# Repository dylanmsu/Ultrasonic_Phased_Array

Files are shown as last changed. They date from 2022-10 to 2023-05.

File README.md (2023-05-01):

# Ultrasonic_Phased_Array
This repository is under construction and will contain all the sources for a working ultrasonic phased array.
The vitis project in this repository is to be used in a accoustic levitation example.

## Working principle
Lets consider an example where we want to send a single pulse of airpressure to a certain point in space. We have an array of transducers we can work with. Since the waves travel in a sphere around the transducers, we can time the pulses at each transducer in such a way that all the wavefronts arrive at the same time in a single focal point. This is illustrated in the animation below.

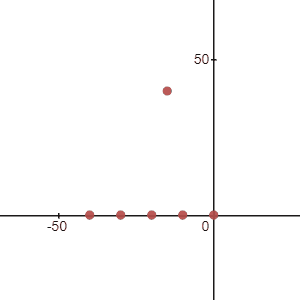
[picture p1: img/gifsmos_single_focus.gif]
[]()

If we were to send a sinewave with the same delay through the transducers instead of a single pulse, all the peaks and troughs of those waves would ideally only add up in the focal point. The amplitude would then be the greatest at that point and ideally cancel out everywhere else. This is actually not always the case because a side effect of using a periodic signal is that we create te posibility of sidelobes. Sidelobes are areas where some of the sinewaves constructively add up unwantedly where the phase shift is a multiple of 360 degrees. To prevent the occurance of sidelobes, we need to space the transducers with a distance between 1/2 wavelength, and 1/4 wavelength. 

To calculate the phase offsets per transducer for a single focal point, the following formula is used:
$$\varphi =  -\frac{2\pi\sqrt{(X_t - X_f)^2 + (Y_t - Y_f)^2 + (Z_t - Z_f)^2}}{\lambda}$$
Where: 
- $\varphi$ = the phase offset for a given transducer
- $X_t, Y_t, Z_t$ = the location of the transducer
- $X_f, Y_f, Z_f$ = the location of the focal point
- $\lambda$ = wavelength

The waves exiting the transducers will look something like this.

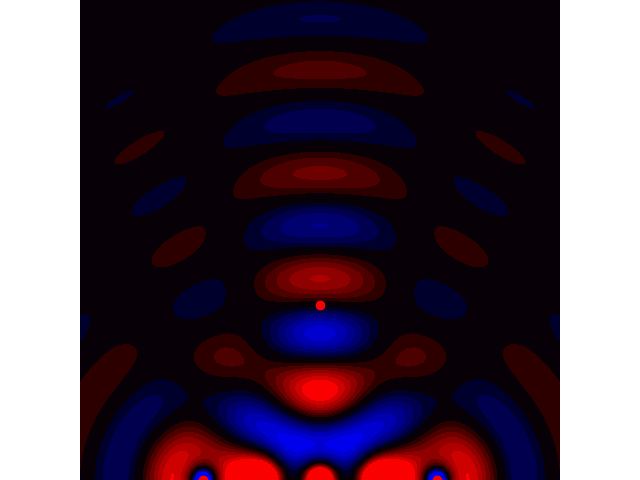
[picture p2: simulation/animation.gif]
[]()

The red dots at the bottom are sources emitting pure sinusodial signals with an adjusted phase delay so all the waves are in phase at the red dot around the middle.

There is an included python script called 'wave_equation.py' that focuses the waves to your mouse location by manipulating the phases of the emitters. It solves the 2d wave equation so it should be more acurate than the above animation.

We can also steer a beam into a specified direction. To do this we have to align the wavefronts into a plane where its normal vector points to the direction of travel. This is illustrated in 2d in the animation below. 

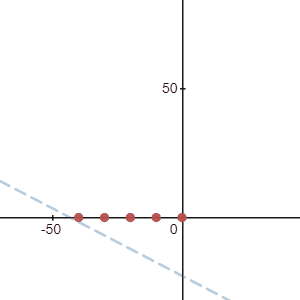
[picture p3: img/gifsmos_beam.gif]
[]()

Here the phase offsets are calculated using the following formula:
$$\varphi = \frac{2\pi(aX_t+bY_t-Z_t)}{\lambda\sqrt{1+a^2+b^2}}$$
Where: 
- $\varphi$ = the phase offset for a given transducer
- $X_t, Y_t, Z_t$ = the location of the transducer
- $a$ = the slope of the tangent plane in the x-axis
- $b$ = the slope of the tangent plane in the y-axis
- $\lambda$ = wavelength

The waves exiting the transducers will look something like this.

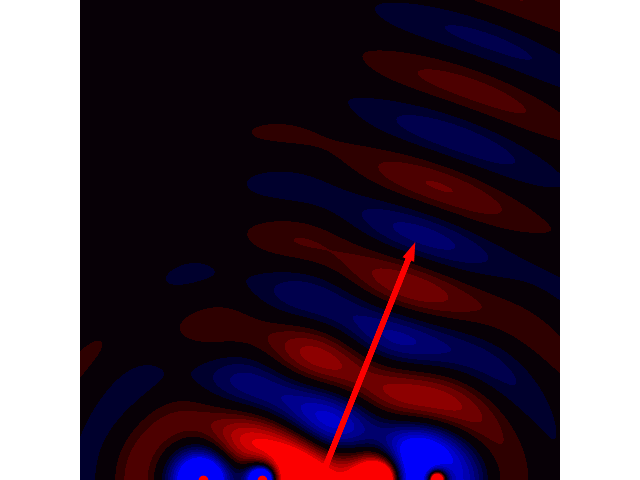
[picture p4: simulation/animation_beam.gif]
[]()

In the case for this project, the spacing between the sources is 10 mm wich is more than double the recommended wavelength so we expect some loss of energy through sidelobes. Even more so diagonally since the sources are placed in a rectangular grid and the diagonal spacing is 14.14 mm. Placing the sources in a hexagonal grid solves big diagonal spacing but this makes the design of the PCB more challanging. For this reason i opted to design a rectangular grid of sources anyway.

## Setup
There are two array's used in the levitation example. One is facing upwards and the other is facing downwards. They are facing eachother with a distance of 70mm. This distance is arbitrarily chosen based on the needed volume for levitation.

## FPGA
The FPGA used in this project is the ZYNQ XC7Z020 on a Zybo Z7 board but any Zynq FPGA should work. The FPGA contains two distinct parts: The processing system (PS) and the programmable logic (PL):

### Programmable Logic
The PL contains an implementation which receives 7 bit values from the PS (Processing System) for every transducer. This value sets the phase of the output signal. This is acheived by making a fifo of length = 2^7 in the case of a phase resolution of 7 bits. The 40KHz signal is fed into the fifo at 40KHz * 2^7 = 5.12MHz. The reason for this is because we want exactly 1 full period of the signal in the fifo. The 7 bit value determines at which address of the fifo the output signal is tapped from. This way wan can adjust the phase of the output signal in 2^7 steps per period.

The block diagram that takes an AXI peripheral bus and outputs a serial data stream to drive the included transducer board is illustrated below. 

[]()

here is an overview of the in- and output signals:
- **signal_in**: this is the signal that will drive the transducers and whos phase will be altered, in our case this signal would have a 50% dutycycle at 40KHz.
- **fifo_clk**: this is the clock that shifts the fifo's used for the delay generation. This should be 2^7 times faster than the 40KHz signal. in this case the fifo length and so the phase resolution is 2^7. This means a frequency of 5.12MHz.
- **ser_clk**: this is the serial clock that drives the serializer and also the shift registers on the transducer board. This clock should be 5x the 'fifo_clock' if each shift register drives 5 transducers. This means a frequency of 25.6MHz.
- **s00_axi_aclk**: this is the AXI peripheral clock comming directly from the Processing system.
- **en**: enable the output signal.
- **resetn**: active low reset signal.
- **S00_AXI**: AXI slave port
- **pmod_out**: this port goes directly to a Pmod port on the FPGA-board and drives the transducer board.

The AXI peripheral IP_block generates the delayed signals and outputs them as a 25 bit vector. This vector is split into 5x 5 bit vectors by the xlslice blocks. The 5 bit vectors enter the seializer. The data is then clocked bit by bit to the output.

### Implementation
[]()

TODO

### Processing System
The Processing system sends data to the FPGA facric which adjusts the phase offsets of the physical transducers.

### Practical limitations
In an ideal world the signal applied to the physical transducer should give the same signal in air pressure. That is however not the case. For every transducer there is a significant random phase shift present. This will completely negate our effort to acheive a phased array. So we have to measure the phase shift of every transducer and incorporate this into the phase calculations.

### Video
Below is a video showing two ultrasonic arrays levitating a piece of styrofoam in an preprogrammed path.
<a href="http://www.youtube.com/watch?feature=player_embedded&v=-Alf5AHHJVo" target="_blank">
 Watch the video
</a>

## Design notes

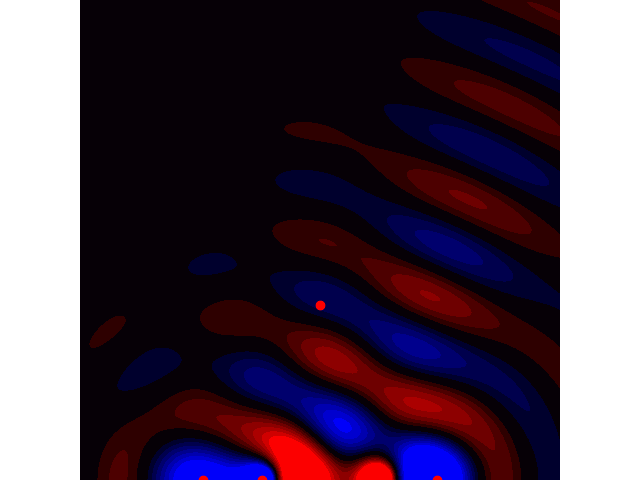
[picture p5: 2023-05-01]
animation_beam.gif

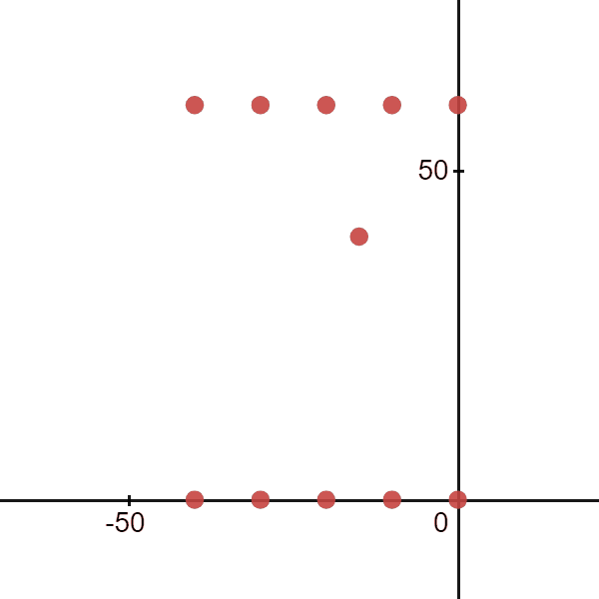
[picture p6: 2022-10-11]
img/gifsmos_double_focus.gif

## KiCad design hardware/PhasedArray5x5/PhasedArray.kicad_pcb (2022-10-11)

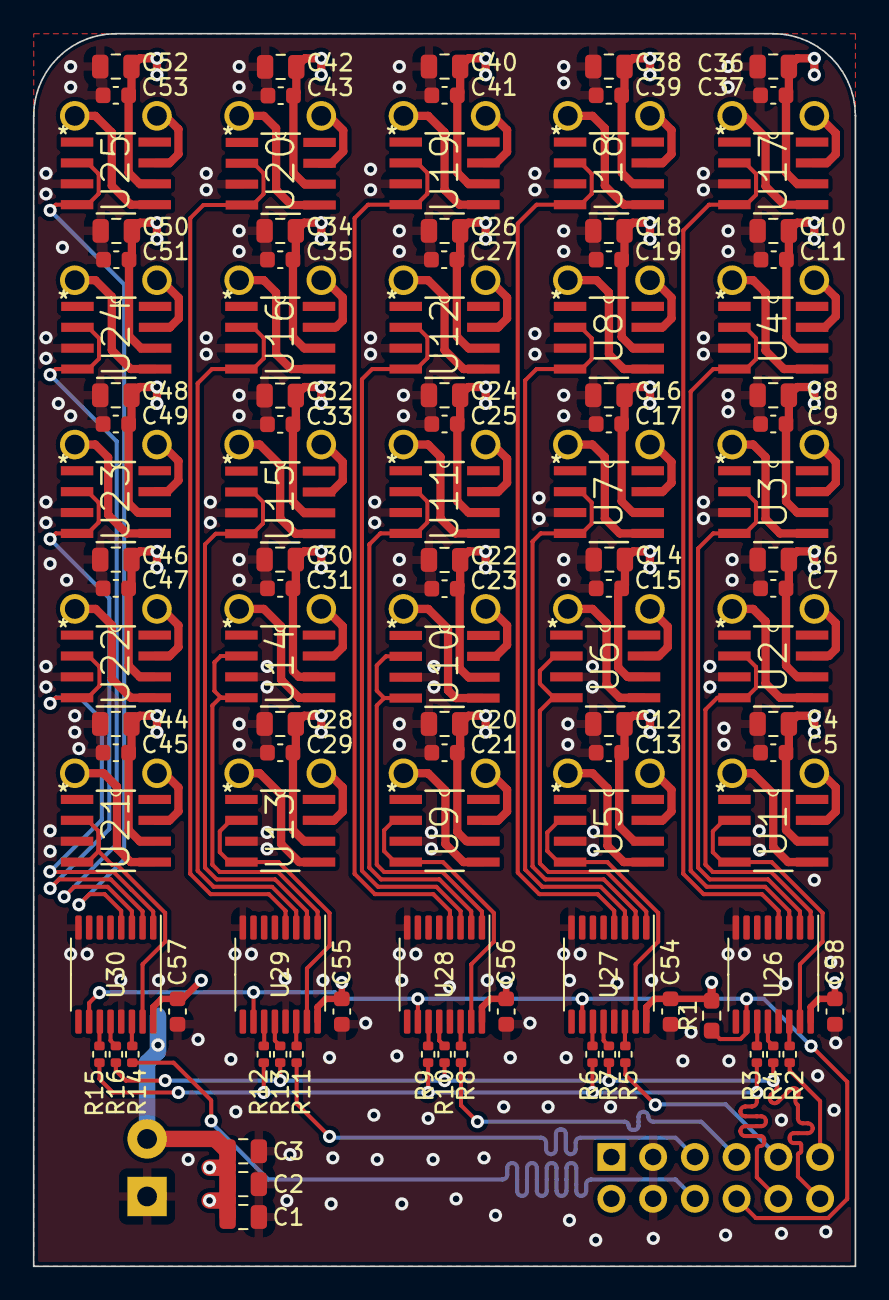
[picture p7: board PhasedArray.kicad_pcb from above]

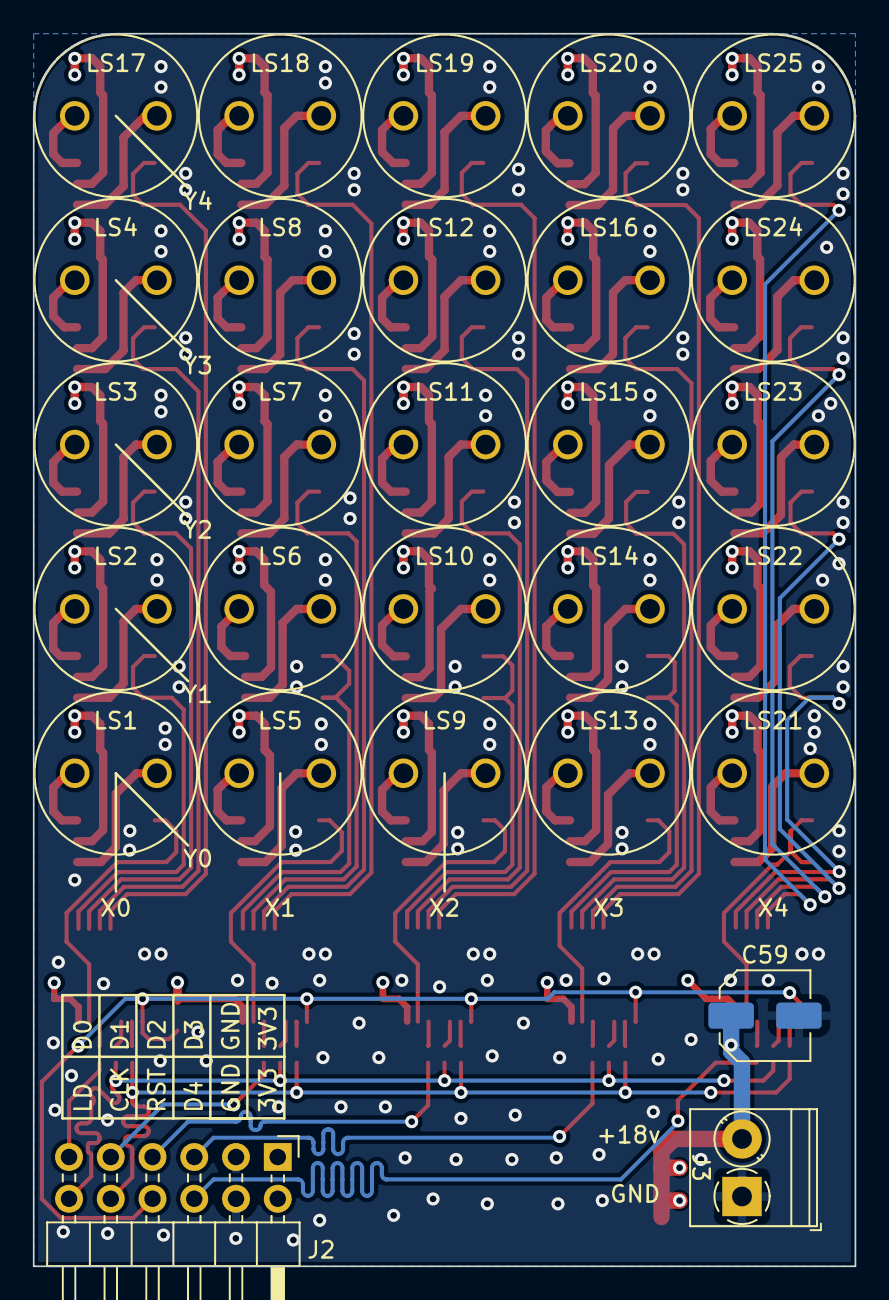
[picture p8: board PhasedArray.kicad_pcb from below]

Board: 4 copper layers, 50.0 x 75.0 mm, 132 parts (28 on the bottom side), 101 nets.

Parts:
C1, C2, C3, C4, C6, C8, C10, C12, C14, C16, C18, C20, C22, C24, C26, C28, C30, C32, C34, C36, C38, C40, C42, C44, C46, C48, C50, C52: 4.7uF; C_0805_2012Metric
C5, C7, C9, C11, C13, C15, C17, C19, C21, C23, C25, C27, C29, C31, C33, C35, C37, C39, C41, C43, C45, C47, C49, C51, C53, C54, C55, C56, C57, C58: 100nF; C_0603_1608Metric
C59: 47uF; C_Elec_5x5.4
J2: Conn_02x06_Odd_Even; PinHeader_2x06_P2.54mm_Horizontal
J3: Screw_Terminal_01x02; TerminalBlock_Phoenix_PT-1,5-2-3.5-H_1x02_P3.50mm_Horizontal
LS1, LS2, LS3, LS4, LS5, LS6, LS7, LS8, LS9, LS10, LS11, LS12, LS13, LS14, LS15, LS16, LS17, LS18, LS19, LS20, LS21, LS22, LS23, LS24, LS25: Speaker_Ultrasound; XDCR_MA40S4R
R1: 0R; R_0603_1608Metric_Pad0.98x0.95mm_HandSolder
R2, R3, R4, R5, R6, R7, R8, R9, R10, R11, R12, R13, R14, R15, R16: 39R; R_0402_1005Metric
U1, U2, U3, U4, U5, U6, U7, U8, U9, U10, U11, U12, U13, U14, U15, U16, U17, U18, U19, U20, U21, U22, U23, U24, U25: TC4428AEOA; SOIC127P600X175-8N
U26, U27, U28, U29, U30: 74AHCT595; TSSOP-16_4.4x5mm_P0.65mm

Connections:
+3V3: C54.1, C55.1, C56.1, C57.1, C58.1, J2.1, J2.2, R1.2, U26.16 (VCC), U27.16 (VCC), U28.16 (VCC), U29.16 (VCC), U30.16 (VCC)
+15V: C1.1, C2.1, C3.1, C4.1, C5.1, C6.1, C7.1, C8.1, C9.1, C10.1, C11.1, C12.1, C13.1, C14.1, C15.1, C16.1, C17.1, C18.1, C19.1, C20.1, C21.1, C22.1, C23.1, C24.1, C25.1, C26.1, C27.1, C28.1, C29.1, C30.1, C31.1, C32.1, C33.1, C34.1, C35.1, C36.1, C37.1, C38.1, C39.1, C40.1, C41.1, C42.1, C43.1, C44.1, C45.1, C46.1, C47.1, C48.1, C49.1, C50.1, C51.1, C52.1, C53.1, C59.1, J3.2, U1.6 (VDD), U2.6 (VDD), U3.6 (VDD), U4.6 (VDD), U5.6 (VDD), U6.6 (VDD), U7.6 (VDD), U8.6 (VDD), U9.6 (VDD), U10.6 (VDD), U11.6 (VDD), U12.6 (VDD), U13.6 (VDD), U14.6 (VDD), U15.6 (VDD), U16.6 (VDD), U17.6 (VDD), U18.6 (VDD), U19.6 (VDD), U20.6 (VDD), U21.6 (VDD), U22.6 (VDD), U23.6 (VDD), U24.6 (VDD), U25.6 (VDD)
CLK: J2.10, R3.1, R6.1, R9.1, R12.1, R15.1
GND: C1.2, C2.2, C3.2, C4.2, C5.2, C6.2, C7.2, C8.2, C9.2, C10.2, C11.2, C12.2, C13.2, C14.2, C15.2, C16.2, C17.2, C18.2, C19.2, C20.2, C21.2, C22.2, C23.2, C24.2, C25.2, C26.2, C27.2, C28.2, C29.2, C30.2, C31.2, C32.2, C33.2, C34.2, C35.2, C36.2, C37.2, C38.2, C39.2, C40.2, C41.2, C42.2, C43.2, C44.2, C45.2, C46.2, C47.2, C48.2, C49.2, C50.2, C51.2, C52.2, C53.2, C54.2, C55.2, C56.2, C57.2, C58.2, C59.2, J2.3, J2.4, J3.1, U1.3 (GND), U2.3 (GND), U3.3 (GND), U4.3 (GND), U5.3 (GND), U6.3 (GND), U7.3 (GND), U8.3 (GND), U9.3 (GND), U10.3 (GND), U11.3 (GND), U12.3 (GND), U13.3 (GND), U14.3 (GND), U15.3 (GND), U16.3 (GND), U17.3 (GND), U18.3 (GND), U19.3 (GND), U20.3 (GND), U21.3 (GND), U22.3 (GND), U23.3 (GND), U24.3 (GND), U25.3 (GND), U26.8 (GND), U26.13 (~OE), U27.8 (GND), U27.13 (~OE), U28.8 (GND), U28.13 (~OE), U29.8 (GND), U29.13 (~OE), U30.8 (GND), U30.13 (~OE)
LOAD: J2.12, R4.1, R7.1, R10.1, R13.1, R16.1
unnamed: LS1.1, U1.7 (*OUT_A)
unnamed: LS1.2, U1.5 (*OUT_B)
unnamed: LS2.1, U2.7 (*OUT_A)
unnamed: LS2.2, U2.5 (*OUT_B)
unnamed: LS3.1, U3.7 (*OUT_A)
unnamed: LS3.2, U3.5 (*OUT_B)
unnamed: LS4.1, U4.7 (*OUT_A)
unnamed: LS4.2, U4.5 (*OUT_B)
unnamed: LS5.1, U5.7 (*OUT_A)
unnamed: LS5.2, U5.5 (*OUT_B)
unnamed: LS6.1, U6.7 (*OUT_A)
unnamed: LS6.2, U6.5 (*OUT_B)
unnamed: LS7.1, U7.7 (*OUT_A)
unnamed: LS7.2, U7.5 (*OUT_B)
unnamed: LS8.1, U8.7 (*OUT_A)
unnamed: LS8.2, U8.5 (*OUT_B)
unnamed: LS9.1, U9.7 (*OUT_A)
unnamed: LS9.2, U9.5 (*OUT_B)
unnamed: LS10.1, U10.7 (*OUT_A)
unnamed: LS10.2, U10.5 (*OUT_B)
unnamed: LS11.1, U11.7 (*OUT_A)
unnamed: LS11.2, U11.5 (*OUT_B)
unnamed: LS12.1, U12.7 (*OUT_A)
unnamed: LS12.2, U12.5 (*OUT_B)
unnamed: LS13.1, U13.7 (*OUT_A)
unnamed: LS13.2, U13.5 (*OUT_B)
unnamed: LS14.1, U14.7 (*OUT_A)
unnamed: LS14.2, U14.5 (*OUT_B)
unnamed: LS15.1, U15.7 (*OUT_A)
unnamed: LS15.2, U15.5 (*OUT_B)
unnamed: LS16.1, U16.7 (*OUT_A)
unnamed: LS16.2, U16.5 (*OUT_B)
unnamed: LS17.1, U17.7 (*OUT_A)
unnamed: LS17.2, U17.5 (*OUT_B)
unnamed: LS18.1, U18.7 (*OUT_A)
unnamed: LS18.2, U18.5 (*OUT_B)
unnamed: LS19.1, U19.7 (*OUT_A)
unnamed: LS19.2, U19.5 (*OUT_B)
unnamed: LS20.1, U20.7 (*OUT_A)
unnamed: LS20.2, U20.5 (*OUT_B)
unnamed: LS21.1, U21.7 (*OUT_A)
unnamed: LS21.2, U21.5 (*OUT_B)
unnamed: LS22.1, U22.7 (*OUT_A)
unnamed: LS22.2, U22.5 (*OUT_B)
unnamed: LS23.1, U23.7 (*OUT_A)
unnamed: LS23.2, U23.5 (*OUT_B)
unnamed: LS24.1, U24.7 (*OUT_A)
unnamed: LS24.2, U24.5 (*OUT_B)
unnamed: LS25.1, U25.7 (*OUT_A)
unnamed: LS25.2, U25.5 (*OUT_B)
unnamed: R3.2, U26.11 (SRCLK)
unnamed: R4.2, U26.12 (RCLK)
unnamed: R2.2, U26.14 (SER)
unnamed: R6.2, U27.11 (SRCLK)
unnamed: R7.2, U27.12 (RCLK)
unnamed: R5.2, U27.14 (SER)
unnamed: R9.2, U28.11 (SRCLK)
unnamed: R10.2, U28.12 (RCLK)
unnamed: R8.2, U28.14 (SER)
unnamed: R12.2, U29.11 (SRCLK)
unnamed: R13.2, U29.12 (RCLK)
unnamed: R11.2, U29.14 (SER)
unnamed: R15.2, U30.11 (SRCLK)
unnamed: R16.2, U30.12 (RCLK)
unnamed: R14.2, U30.14 (SER)
RESET: J2.8, R1.1, U26.10 (~SRCLR), U27.10 (~SRCLR), U28.10 (~SRCLR), U29.10 (~SRCLR), U30.10 (~SRCLR)
SER0: J2.11, R2.1
SER1: J2.9, R5.1
SER2: J2.7, R8.1
SER3: J2.5, R11.1
SER4: J2.6, R14.1
input00: U1.2 (IN_A), U1.4 (IN_B), U26.15 (QA)
input01: U2.2 (IN_A), U2.4 (IN_B), U26.1 (QB)
input02: U3.2 (IN_A), U3.4 (IN_B), U26.2 (QC)
input03: U4.2 (IN_A), U4.4 (IN_B), U26.3 (QD)
input04: U17.2 (IN_A), U17.4 (IN_B), U26.4 (QE)
input10: U5.2 (IN_A), U5.4 (IN_B), U27.15 (QA)
input11: U6.2 (IN_A), U6.4 (IN_B), U27.1 (QB)
input12: U7.2 (IN_A), U7.4 (IN_B), U27.2 (QC)
input13: U8.2 (IN_A), U8.4 (IN_B), U27.3 (QD)
input14: U18.2 (IN_A), U18.4 (IN_B), U27.4 (QE)
input20: U9.2 (IN_A), U9.4 (IN_B), U28.15 (QA)
input21: U10.2 (IN_A), U10.4 (IN_B), U28.1 (QB)
input22: U11.2 (IN_A), U11.4 (IN_B), U28.2 (QC)
input23: U12.2 (IN_A), U12.4 (IN_B), U28.3 (QD)
input24: U19.2 (IN_A), U19.4 (IN_B), U28.4 (QE)
input30: U13.2 (IN_A), U13.4 (IN_B), U29.15 (QA)
input31: U14.2 (IN_A), U14.4 (IN_B), U29.1 (QB)
input32: U15.2 (IN_A), U15.4 (IN_B), U29.2 (QC)
input33: U16.2 (IN_A), U16.4 (IN_B), U29.3 (QD)
input34: U20.2 (IN_A), U20.4 (IN_B), U29.4 (QE)
input40: U21.2 (IN_A), U21.4 (IN_B), U30.15 (QA)
input41: U22.2 (IN_A), U22.4 (IN_B), U30.1 (QB)
input42: U23.2 (IN_A), U23.4 (IN_B), U30.2 (QC)
input43: U24.2 (IN_A), U24.4 (IN_B), U30.3 (QD)
input44: U25.2 (IN_A), U25.4 (IN_B), U30.4 (QE)

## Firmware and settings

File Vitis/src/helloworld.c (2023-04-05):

/*
 * helloworld.c: simple test application
 *
 * This application configures UART 16550 to baud rate 9600.
 * PS7 UART (Zynq) is not initialized by this application, since
 * bootrom/bsp configures it to baud rate 115200
 *
 * ------------------------------------------------
 * | UART TYPE   BAUD RATE                        |
 * ------------------------------------------------
 *   uartns550   9600
 *   uartlite    Configurable only in HW design
 *   ps7_uart    115200 (configured by bootrom/bsp)
 */

#include <stdio.h>
#include "platform.h"
#include "xil_printf.h"
#include "xparameters.h"
#include <unistd.h>
#include "axi_delay_generator.h"
#include "xil_io.h"
#include "xgpio.h"
#include <math.h>

// math constants
#define PI 				3.1415926		//PI

// parameters defined in fpga fabric
#define FREQ			40000			//carrier frequency for the transducers
#define RESOLUTION 		128				//resolution in mm in which the phases can be adjusted.

// array pcb parameters
#define WIDTH 			5				//number of transducers in the x direction
#define HEIGTH 			5				//number of transducers in the y direction
#define DISTANCE		10.0			//distance between the transducers

// environment parameters
#define TEMPERATURE 	20.0			//ambient temperature used to calculate wavelength

// accoustic lefitation example
#define MOVEMENT_RES	10				//movement resolution in steps/mm
#define ARRAY_DISTANCE	70				//distance between the top and bottom array

// calculate wavelength in air based on temperature and frequency
double wavelength = (331000*sqrt(1 + TEMPERATURE/273.0))/FREQ; //in mm

XGpio gpio_0;

int phases[1][WIDTH][HEIGTH] = {0};

int offsets[2][5][5] = {
		{{128-28, 128-105,  128-44,  128-108,  128-36},
		{128-44,  128-105,  128-46, 128-38, 128-100},
		{128-38, 128-38,  128-38,  128-41, 128-110},
		{128-44, 128-113,  128-113, 128-97, 128-38},
		{128-30,  128-51, 128-38,  128-49,  128-110}},//*/

		{{128-113, 128-41,  128-92,  128-23,  128-105},
		{128-46,  128-97,  128-110, 128-110, 128-41},
		{128-113, 128-92,  128-46,  128-113, 128-36},
		{128-102, 128-33,  128-110, 128-113, 128-97},
		{128-41,  128-108, 128-44,  128-51,  128-100}}//*/
};

int reg_addresses[25] = {
		AXI_DELAY_GENERATOR_S00_AXI_SLV_REG0_OFFSET,
		AXI_DELAY_GENERATOR_S00_AXI_SLV_REG1_OFFSET,
		AXI_DELAY_GENERATOR_S00_AXI_SLV_REG2_OFFSET,
		AXI_DELAY_GENERATOR_S00_AXI_SLV_REG3_OFFSET,
		AXI_DELAY_GENERATOR_S00_AXI_SLV_REG4_OFFSET,
		AXI_DELAY_GENERATOR_S00_AXI_SLV_REG5_OFFSET,
		AXI_DELAY_GENERATOR_S00_AXI_SLV_REG6_OFFSET,
		AXI_DELAY_GENERATOR_S00_AXI_SLV_REG7_OFFSET,
		AXI_DELAY_GENERATOR_S00_AXI_SLV_REG8_OFFSET,
		AXI_DELAY_GENERATOR_S00_AXI_SLV_REG9_OFFSET,
		AXI_DELAY_GENERATOR_S00_AXI_SLV_REG10_OFFSET,
		AXI_DELAY_GENERATOR_S00_AXI_SLV_REG11_OFFSET,
		AXI_DELAY_GENERATOR_S00_AXI_SLV_REG12_OFFSET,
		AXI_DELAY_GENERATOR_S00_AXI_SLV_REG13_OFFSET,
		AXI_DELAY_GENERATOR_S00_AXI_SLV_REG14_OFFSET,
		AXI_DELAY_GENERATOR_S00_AXI_SLV_REG15_OFFSET,
		AXI_DELAY_GENERATOR_S00_AXI_SLV_REG16_OFFSET,
		AXI_DELAY_GENERATOR_S00_AXI_SLV_REG17_OFFSET,
		AXI_DELAY_GENERATOR_S00_AXI_SLV_REG18_OFFSET,
		AXI_DELAY_GENERATOR_S00_AXI_SLV_REG19_OFFSET,
		AXI_DELAY_GENERATOR_S00_AXI_SLV_REG20_OFFSET,
		AXI_DELAY_GENERATOR_S00_AXI_SLV_REG21_OFFSET,
		AXI_DELAY_GENERATOR_S00_AXI_SLV_REG22_OFFSET,
		AXI_DELAY_GENERATOR_S00_AXI_SLV_REG23_OFFSET,
		AXI_DELAY_GENERATOR_S00_AXI_SLV_REG24_OFFSET
};

int ip_base_addresses[2] = {
		XPAR_GENERATOR_1_AXI_DELAY_GENERATOR_1_S00_AXI_BASEADDR,
		XPAR_GENERATOR_2_AXI_DELAY_GENERATOR_1_S00_AXI_BASEADDR
};

void write_phase(int idx, int x, int y, uint8_t phase) {
	int i = (x)*5 + (4-y);
	AXI_DELAY_GENERATOR_mWriteReg(ip_base_addresses[idx], reg_addresses[i], phase%RESOLUTION);
}

void writePhases() {
	for (int i=0; i<WIDTH; i++) {
		for (int j=0; j<HEIGTH; j++) {
			for (int k=0; k<2; k++) {
				write_phase(k, i, j, phases[k][i][j] + offsets[k][4-i][4-j]);
			}
		}
	}
}

void setFocusPoint(int idx, double x, double y, double z) {
	for (int i=0; i<WIDTH; i++) {
		for (int j=0; j<HEIGTH; j++) {
			double phase = sqrt((i*DISTANCE-x)*(i*DISTANCE-x) + (y)*(y) + (j*DISTANCE-z)*(j*DISTANCE-z));
			phases[idx][i][j] = round((RESOLUTION - 1) - fmod(phase*(RESOLUTION/wavelength), RESOLUTION));
			//phases[idx][i][j] += offsets[idx][4-i][4-j];
		}
	}
}

void levitate(double x, double y, double z) {
	setFocusPoint(0, x + 20, y + ARRAY_DISTANCE/2, z + 20);
	setFocusPoint(1, 4*DISTANCE - (x + 20), ARRAY_DISTANCE - (y + ARRAY_DISTANCE/2), z + 20);
}

int main()
{
	init_platform();

	int status;

	status = XGpio_Initialize(&gpio_0, XPAR_AXI_GPIO_0_DEVICE_ID);
	if (status != XST_SUCCESS) {
		print("paripheral GPIO 0 fail\r\n");
	} else {
		print("paripheral GPIO 0 success\r\n");
	}

	setFocusPoint(1, 20, 35, 20);
	setFocusPoint(0, 20, 35, 20);
	writePhases();

	/*for (int i=0; i<WIDTH; i++) {
		for (int j=0; j<HEIGTH; j++) {
			for (int k=0; k<2; k++) {
				write_phase(k, i, j, offsets[k][4-i][4-j]);
			}
		}
	}*/


	/*for (int i=0; i<25; i++) {
		AXI_DELAY_GENERATOR_mWriteReg(ip_base_addresses[0], reg_addresses[i], i*4);
	}*/

	XGpio_SetDataDirection(&gpio_0, 1, 1);
	XGpio_DiscreteWrite(&gpio_0, 1, 1);

	while (1) {
		XGpio_DiscreteWrite(&gpio_0, 1, 0);
		usleep(10000);
		XGpio_DiscreteWrite(&gpio_0, 1, 1);
		usleep(10000);
	}

    print("Hello World\n\r");
    print("Successfully ran Hello World application");
    cleanup_platform();
    return 0;
}

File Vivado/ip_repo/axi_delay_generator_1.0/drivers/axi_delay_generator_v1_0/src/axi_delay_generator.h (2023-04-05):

#ifndef AXI_DELAY_GENERATOR_H
#define AXI_DELAY_GENERATOR_H


/****************** Include Files ********************/
#include "xil_types.h"
#include "xstatus.h"

#define AXI_DELAY_GENERATOR_S00_AXI_SLV_REG0_OFFSET 0
#define AXI_DELAY_GENERATOR_S00_AXI_SLV_REG1_OFFSET 4
#define AXI_DELAY_GENERATOR_S00_AXI_SLV_REG2_OFFSET 8
#define AXI_DELAY_GENERATOR_S00_AXI_SLV_REG3_OFFSET 12
#define AXI_DELAY_GENERATOR_S00_AXI_SLV_REG4_OFFSET 16
#define AXI_DELAY_GENERATOR_S00_AXI_SLV_REG5_OFFSET 20
#define AXI_DELAY_GENERATOR_S00_AXI_SLV_REG6_OFFSET 24
#define AXI_DELAY_GENERATOR_S00_AXI_SLV_REG7_OFFSET 28
#define AXI_DELAY_GENERATOR_S00_AXI_SLV_REG8_OFFSET 32
#define AXI_DELAY_GENERATOR_S00_AXI_SLV_REG9_OFFSET 36
#define AXI_DELAY_GENERATOR_S00_AXI_SLV_REG10_OFFSET 40
#define AXI_DELAY_GENERATOR_S00_AXI_SLV_REG11_OFFSET 44
#define AXI_DELAY_GENERATOR_S00_AXI_SLV_REG12_OFFSET 48
#define AXI_DELAY_GENERATOR_S00_AXI_SLV_REG13_OFFSET 52
#define AXI_DELAY_GENERATOR_S00_AXI_SLV_REG14_OFFSET 56
#define AXI_DELAY_GENERATOR_S00_AXI_SLV_REG15_OFFSET 60
#define AXI_DELAY_GENERATOR_S00_AXI_SLV_REG16_OFFSET 64
#define AXI_DELAY_GENERATOR_S00_AXI_SLV_REG17_OFFSET 68
#define AXI_DELAY_GENERATOR_S00_AXI_SLV_REG18_OFFSET 72
#define AXI_DELAY_GENERATOR_S00_AXI_SLV_REG19_OFFSET 76
#define AXI_DELAY_GENERATOR_S00_AXI_SLV_REG20_OFFSET 80
#define AXI_DELAY_GENERATOR_S00_AXI_SLV_REG21_OFFSET 84
#define AXI_DELAY_GENERATOR_S00_AXI_SLV_REG22_OFFSET 88
#define AXI_DELAY_GENERATOR_S00_AXI_SLV_REG23_OFFSET 92
#define AXI_DELAY_GENERATOR_S00_AXI_SLV_REG24_OFFSET 96


/**************************** Type Definitions *****************************/
/**
 *
 * Write a value to a AXI_DELAY_GENERATOR register. A 32 bit write is performed.
 * If the component is implemented in a smaller width, only the least
 * significant data is written.
 *
 * @param   BaseAddress is the base address of the AXI_DELAY_GENERATORdevice.
 * @param   RegOffset is the register offset from the base to write to.
 * @param   Data is the data written to the register.
 *
 * @return  None.
 *
 * @note
 * C-style signature:
 * 	void AXI_DELAY_GENERATOR_mWriteReg(u32 BaseAddress, unsigned RegOffset, u32 Data)
 *
 */
#define AXI_DELAY_GENERATOR_mWriteReg(BaseAddress, RegOffset, Data) \
  	Xil_Out32((BaseAddress) + (RegOffset), (u32)(Data))

/**
 *
 * Read a value from a AXI_DELAY_GENERATOR register. A 32 bit read is performed.
 * If the component is implemented in a smaller width, only the least
 * significant data is read from the register. The most significant data
 * will be read as 0.
 *
 * @param   BaseAddress is the base address of the AXI_DELAY_GENERATOR device.
 * @param   RegOffset is the register offset from the base to write to.
 *
 * @return  Data is the data from the register.
 *
 * @note
 * C-style signature:
 * 	u32 AXI_DELAY_GENERATOR_mReadReg(u32 BaseAddress, unsigned RegOffset)
 *
 */
#define AXI_DELAY_GENERATOR_mReadReg(BaseAddress, RegOffset) \
    Xil_In32((BaseAddress) + (RegOffset))

/************************** Function Prototypes ****************************/
/**
 *
 * Run a self-test on the driver/device. Note this may be a destructive test if
 * resets of the device are performed.
 *
 * If the hardware system is not built correctly, this function may never
 * return to the caller.
 *
 * @param   baseaddr_p is the base address of the AXI_DELAY_GENERATOR instance to be worked on.
 *
 * @return
 *
 *    - XST_SUCCESS   if all self-test code passed
 *    - XST_FAILURE   if any self-test code failed
 *
 * @note    Caching must be turned off for this function to work.
 * @note    Self test may fail if data memory and device are not on the same bus.
 *
 */
XStatus AXI_DELAY_GENERATOR_Reg_SelfTest(void * baseaddr_p);

#endif // AXI_DELAY_GENERATOR_H
